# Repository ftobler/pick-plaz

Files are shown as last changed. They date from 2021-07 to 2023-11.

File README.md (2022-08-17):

# pick-plaz
Open source pick and place machine

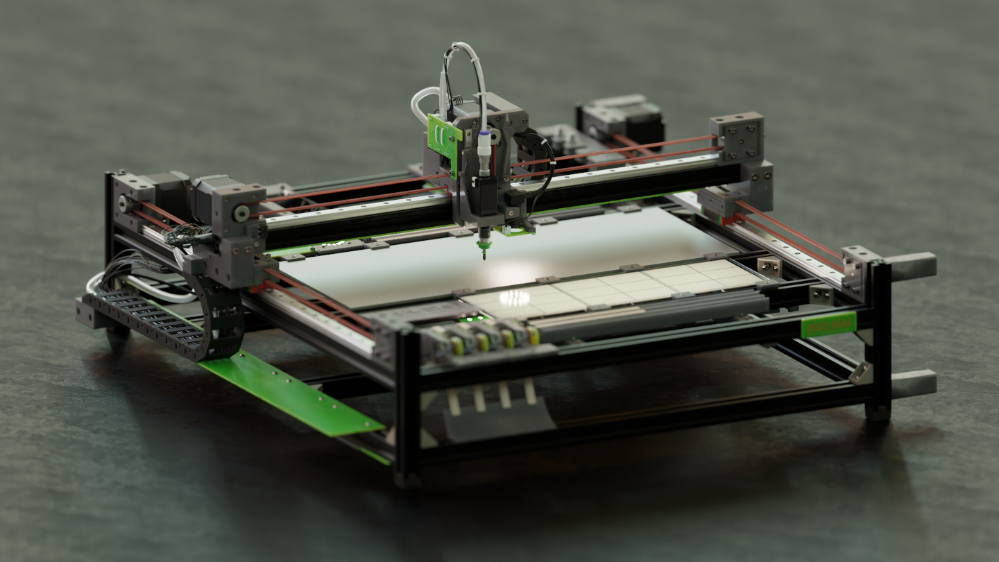
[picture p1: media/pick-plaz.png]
CAD Image Pick-Plaz


[CAD Onshape](https://cad.onshape.com/documents/175bb45940c329c46a77df39/w/56e16a8885c2fef63520b9e2/e/e7ab10496d879b6cf281b14f)

[STEP file repostory (CAD)](https://github.com/ftobler/pick-plaz-cad)

[More Pictures (Imgur)](https://imgur.com/a/lOQ79OQ)

## Issues

* Part preview missing zero point of ICs

# Wishlist

* Camera sharpen menu in UI (laplacian of camera image)

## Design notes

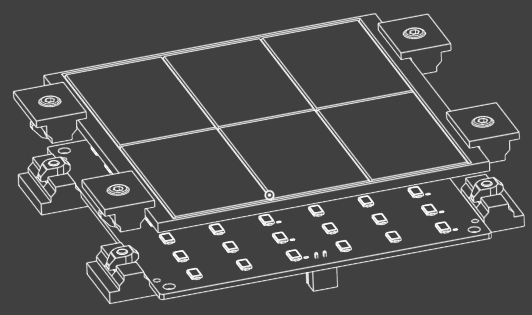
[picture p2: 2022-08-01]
python/web/img/tray.png

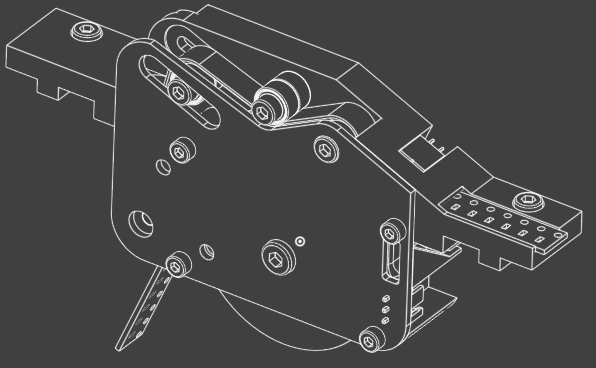
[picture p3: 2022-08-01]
python/web/img/roll.png

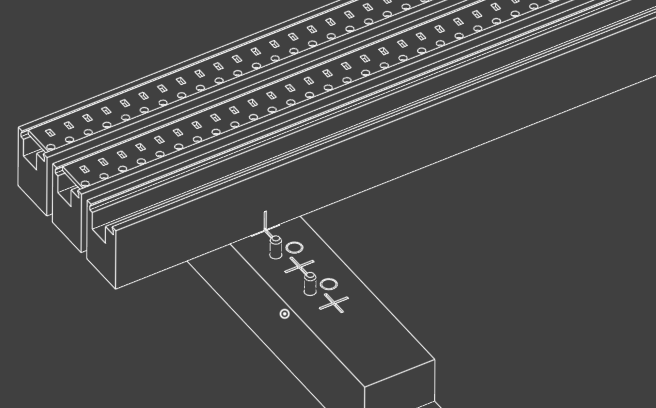
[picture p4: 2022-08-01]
python/web/img/belt.png

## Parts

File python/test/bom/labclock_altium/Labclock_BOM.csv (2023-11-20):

Designator | Quantity | GPV_Number | Description | Manufacturer | Manufacturer Part Number | Footprint
C1, C2 | 2 | 1749.0090 | Cap Cer SMD 10p 50V +/- 0.25pF 0603 C0G | AVX | 06035A100CAT* | C-0603_1608_095_L_RF
C3, C4, C5, C6, C7, C8, C9 | 7 | 1749.0196 | Cap Cer SMD 100n 100V 10% 0603 X7R | MURATA | GRM188R72A104KA35 | C-0603_1608_095_L_RF
D1 | 1 | xxxx.xxxx | IC MCU Cortex M0+ 32K Flash, 8K RAM, 64MHz | ST | STM32G030F6P6 | TSSOP20_N_RF
G1 | 1 | xxxx.xxxx | Crystal Oscillator 32.768kHz 12.5pF �20ppm | ABEL ELECTRON | SMD-3215_2P32.768KHZ12.5PF10PPM | G_3215_N_RF
IC1 | 1 | xxxx.xxxx | IC Converter USB UART | WCN | CH340C | SOIC16_N_RF
R1, R2, R3, R4, R5, R6, R7, R8 | 8 | 1922.0102 | Res SMD 100R 1% 0.1W 0603 | YAGEO | RC0603FR-07100RL | R-0603_1608_050_L_RF
R9, R10, R11, R12, R13, R14, R15, R16, R18, R19, R20, R21, R22, R23, R24, R25, R26, R27, R28, R29, R30, R31, R32, R33, R34, R35 | 26 | 1922.0100 | Res SMD 10k 1% 0.1W 0603 | YAGEO | RC0603FR-0710KL | R-0603_1608_050_L_RF
R17, R36 | 2 | 1922.0011 | Res SMD 1k 1% 0.1W 0603 | YAGEO | RC0603FR-071KL | R-0603_1608_050_L_RF
R37 | 1 | 1922.0140 | Res SMD 100k 1% 0.1W 0603 | YAGEO | RC0603FR-07100KL | R-0603_1608_050_L_RF
U1 | 1 | 1500.7299 | IC REG LDO 3.3V 0.8A SOT223 | Texas Instruments | LM1117MPX-3.3/NOPB | SOT223_L_RF
V1 | 1 | xxxx.xxxx | LED 7-Segment 38mm x 45mm | ? | FJS18101AH | FJS18101AH
V2, V3, V4, V5, V6, V7, V8, V9 | 8 | 1601.0679 | TRANS SMD PNP -45V -0.1A BC807-40 SOT23 | NXP Semiconductors | BC807-40 | SOT23_L_RF
V10 | 1 | 1601.1733 | MOSFET N-CH 50V 200MA SOT-23 | onsemi | BSS138LT1G | SOT23_L_RF
V11, V12, V13, V14, V15, V16, V17, V18, V21 | 9 | 1601.0512 | TRANS SMD NPN 45V 0.1A BC847B SOT23 | NXP Semiconductors | BC847B/C | SOT23_L_RF
V19 | 1 | 1600.2395 | Diode Schottky 20V 0.5A SOD123 | ONSemi | MBR0520LT1G | SOD123_L_RF
V20 | 1 |  | Diode Schottky 1mA 40 Volt | VISHAY | SD101CW-E3-08 | SOD123_L_RF
V29 | 1 | xxxx.xxxx | RGB LED SPI Interface | APA Electronic CO | APA-102-2020-256-8A | V_2020_P6_N_RF
X1, X2 | 2 |  | CONN HEADER 5POS 1ROW THT 2.54MM WE 61300511121 | W�rth Elektronik | 61300511121 | X-0127X0025_R_WE_61300511121
X3 | 1 | xxxx.xxxx | CONN USB-C 16pin | Molex | 105450-0101 | 105450-0101

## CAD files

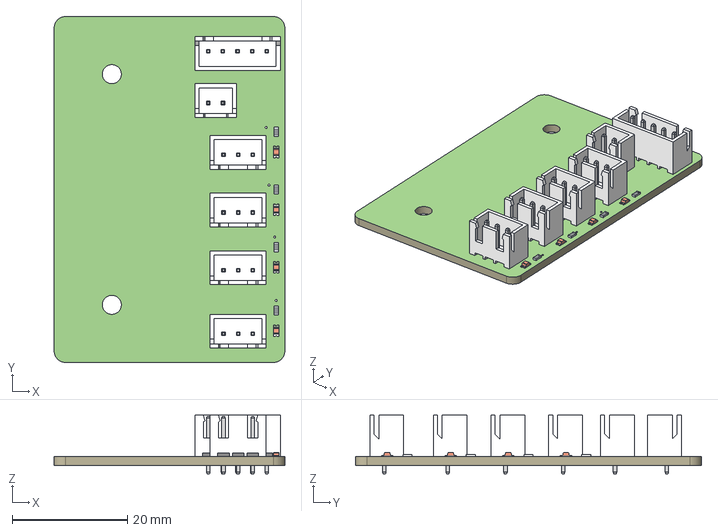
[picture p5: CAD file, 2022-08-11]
pcb/pcb-pick-plaz-feeder-wiring/pcb-pick-plaz-feeder-wiring.step
40.0 x 60.0 x 10.2 mm

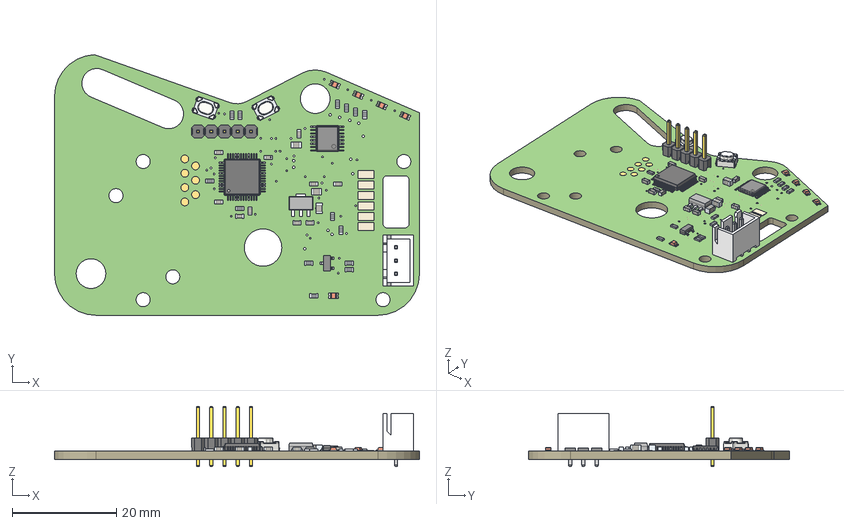
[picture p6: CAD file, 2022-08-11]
pcb/pcb-pick-plaz-feeder/pcb-pick-plaz-feeder.step
70.0 x 50.0 x 11.6 mm

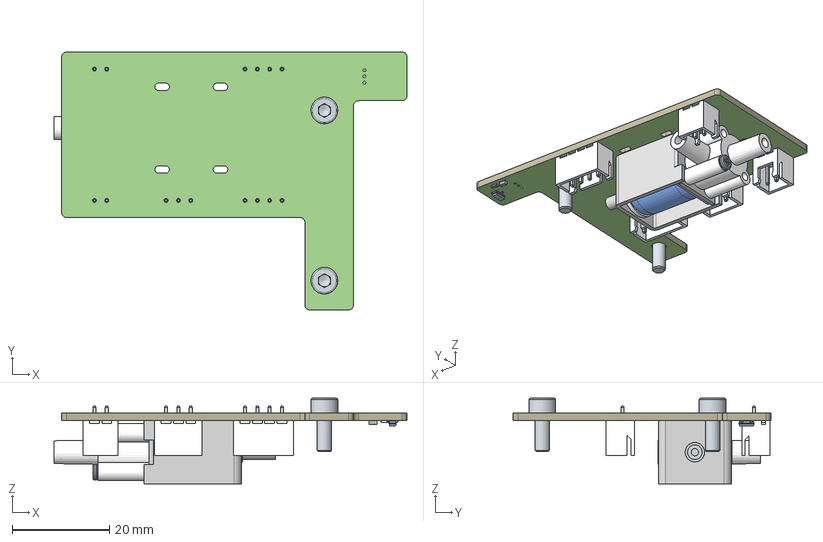
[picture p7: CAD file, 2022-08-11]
pcb/pcb-pick-plaz-hall/pcb hall.step
72.6 x 53.0 x 17.6 mm
Hex socket head cap screw M3x0.50 x 8 x 2
B4B-XH
B3B-XH
Board
B2B-XH
SOT-23
B4B-XH_1
0603-RES
0603_CAP
B2B-XH_1
solenoid valve

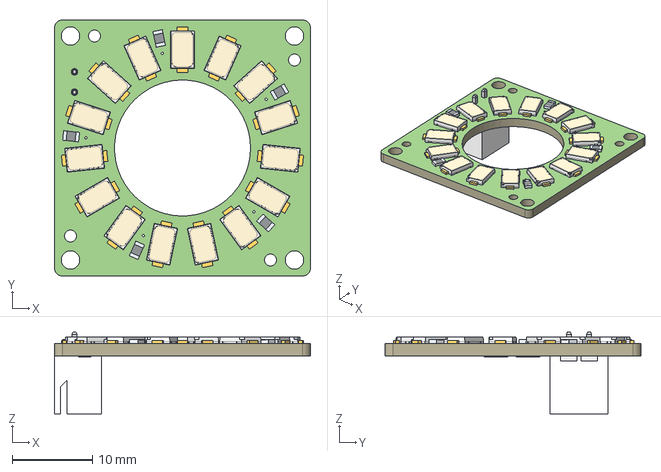
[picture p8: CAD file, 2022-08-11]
pcb/pcb-pick-plaz-ring/pcb-pick-plaz-ring eagle.step
32.0 x 32.0 x 10.2 mm

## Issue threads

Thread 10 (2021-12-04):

Split Screen GUI / Camera

ftobler, 2021-12-04:
Request to add the Option to view the GUI Splitscreen with the camera always on one side of the screen.

8wangyuyang, 2024-04-24:
没有标注用什么上位机软件控制,求软件名。谢谢！

ftobler, 2024-04-28:
Not sure what you mean. The software is the python stuff in this repository. All custom.

8wangyuyang, 2024-04-28:
我的意思是上位机，就像开源的OpenPnP贴片上位机软件。这个是用的是树莓派3B做上位机，用的什么系统或上位机。求大佬资料教程，谢谢！大佬的开源。PCB板已打样，只缺软件控制界面或软件。感谢😊😊😊

8wangyuyang, 2024-04-28:
python调用camera，gui界面 是吗？

ftobler, 2024-04-28:
This is not a OpenPnP build. Python does run on a raspberry pi as host, but you can use other hosts as well. The camera is a standard webcam, the GUI is on the webserver.

8wangyuyang, 2024-04-28:
不支持OpenPNP软件，GUI位于网络服务器是网址或IP地址是吗？

8wangyuyang, 2024-04-28:
我是第一次制作贴片机在树莓派运行的，我安装过klipper不知道一样吗？

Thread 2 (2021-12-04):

Reset Fiducial Placement

ftobler, 2021-12-04:
Request to add a function to reset all fiducial for a new pcb.

ftobler, 2022-07-30:
done

Closed 2022-07-30.

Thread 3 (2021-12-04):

Reset Part Placement

ftobler, 2021-12-04:
Request to add a function to reset part status to place a new pcb

ftobler, 2022-07-30:
done

Closed 2022-07-30.

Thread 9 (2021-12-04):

Improve Auto Assignment of Symbols

ftobler, 2021-12-04:
When PNP and BOM is loaded, the software automatically sets the symbols for the most common package types. This does not work for the following examples:

- SOIC-16

ftobler, 2022-01-23:
in footprints.json there is now a alternative ("alt") list where the parser is looking for a match.

match is made withoug special characters like '-' and '_'

Closed 2022-01-23.

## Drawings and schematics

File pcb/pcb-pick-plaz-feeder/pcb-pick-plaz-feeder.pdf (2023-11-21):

# GND ¹⁰u

## DRV8833PWPR

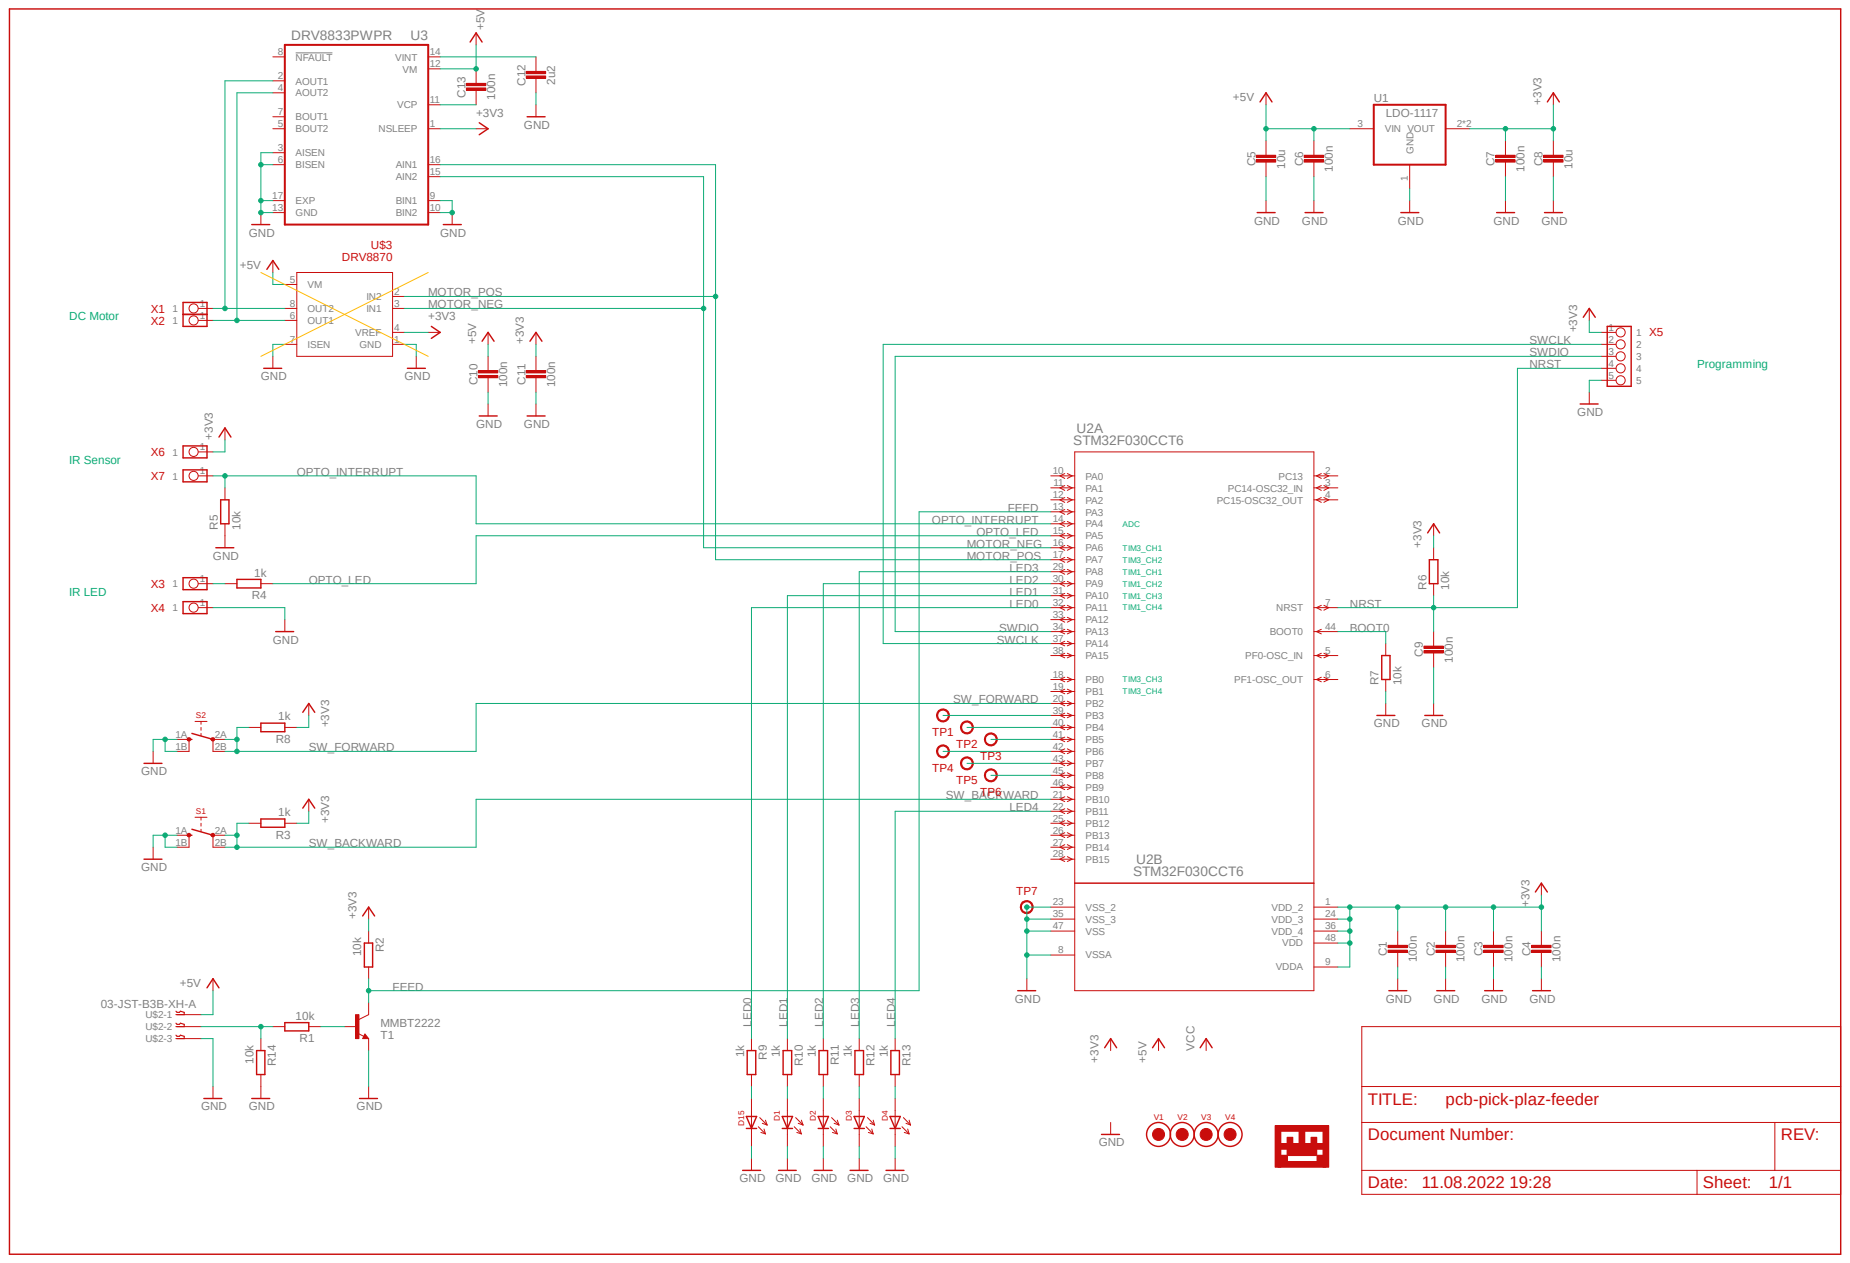
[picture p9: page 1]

MOTOR_NEG | PA6 16
MOTOR_POS | PA7 17

LED3 | PA8 29

PA9 30
PA10 31
PA11 32

SWDIO | PA12 33 PA13 34 | BOOT0

pcb-pick-plaz-feeder

Document Number: | REV:

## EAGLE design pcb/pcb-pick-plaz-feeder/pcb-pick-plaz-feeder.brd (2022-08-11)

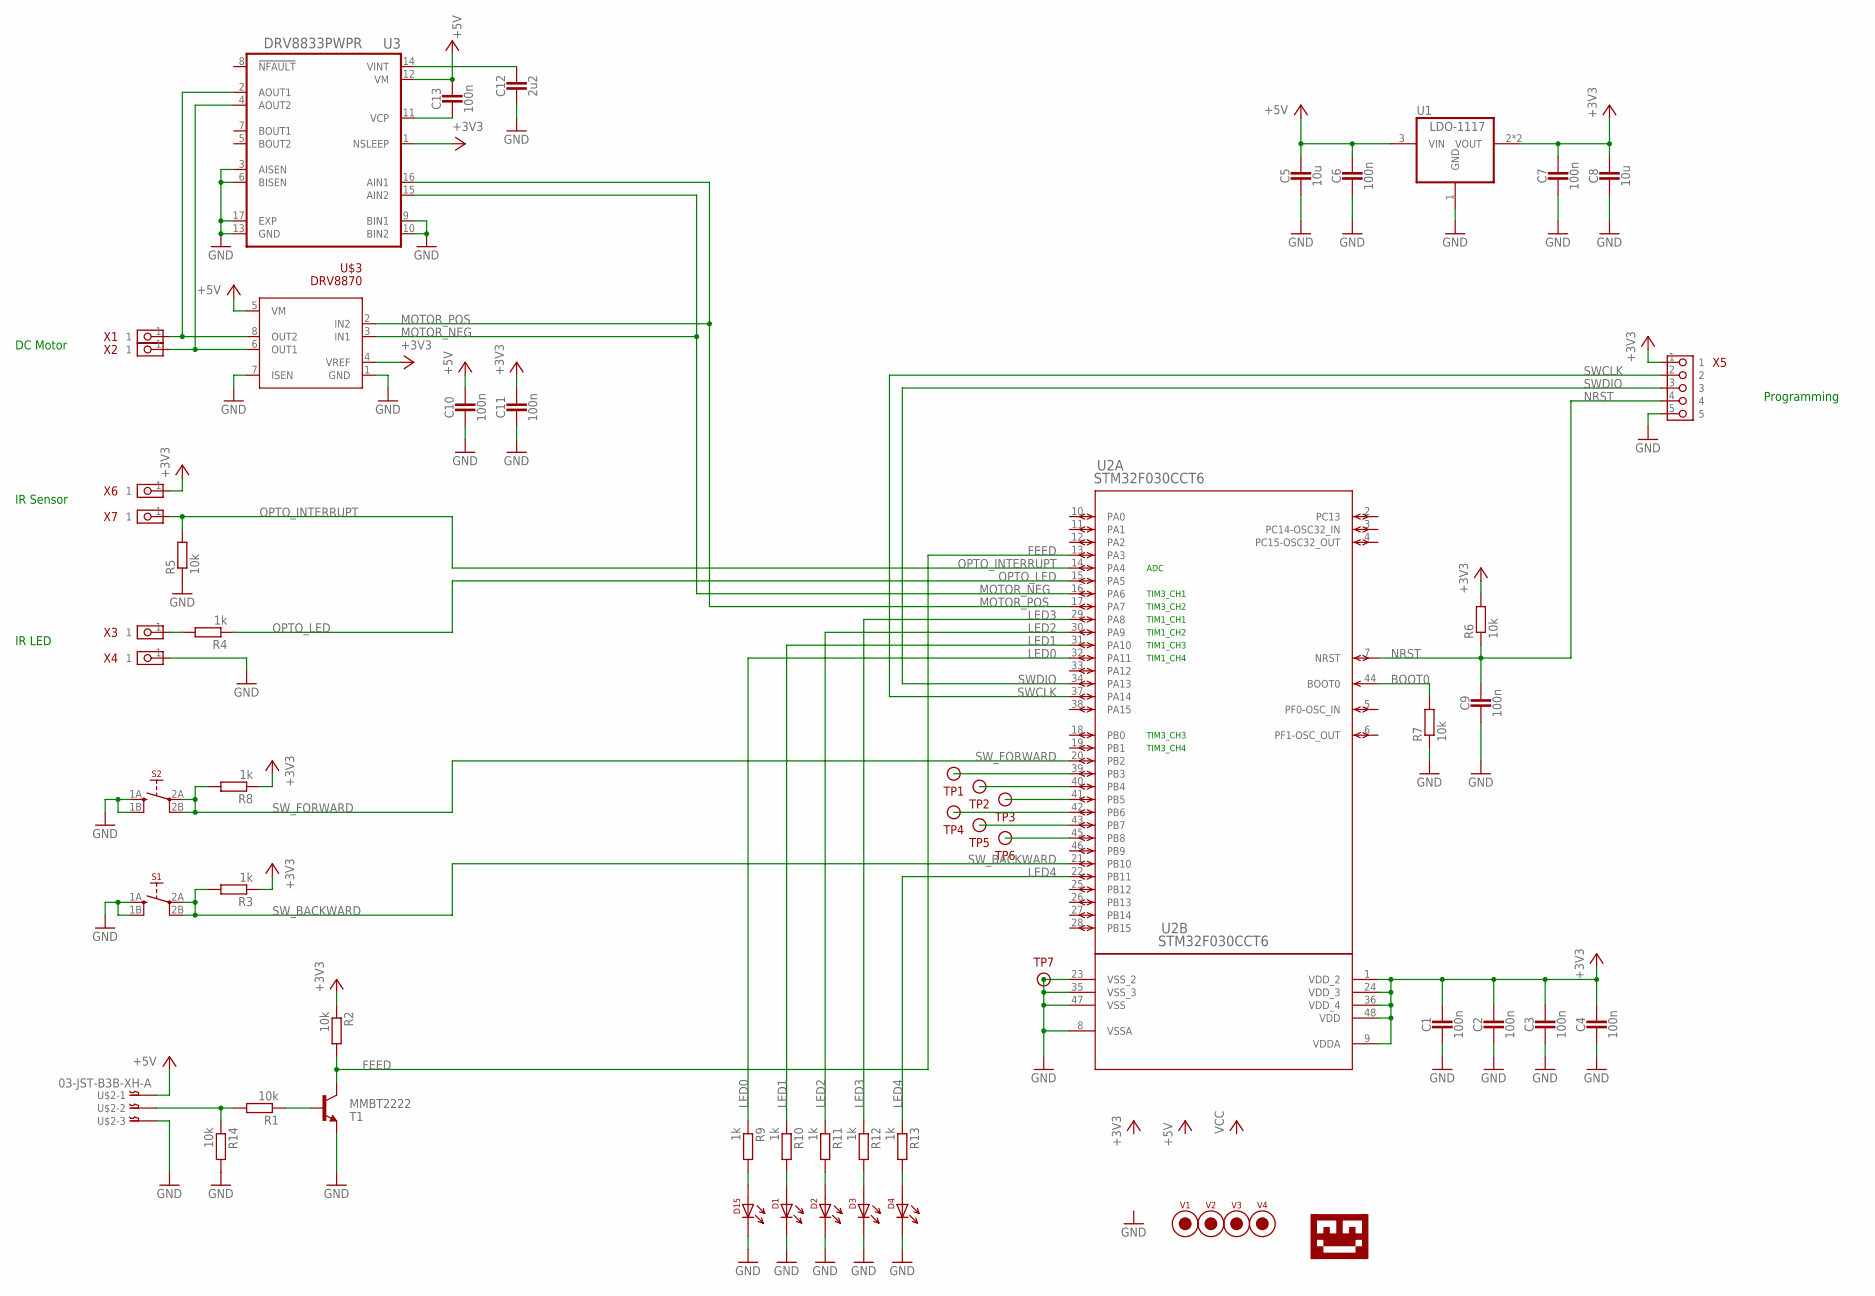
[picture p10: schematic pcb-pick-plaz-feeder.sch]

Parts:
C1, C2, C3, C4, C6, C7, C9, C10, C11, C13: 100n; 0603_CAP
C5, C8: 10u; 0805_CAP
C12: 2u2; 0805_CAP
D1, D2, D3, D4, D15: LED-0805; 0805-DOT
R1, R2, R5, R6, R7, R14: 10k; 0603-RES
R3, R4, R8, R9, R10, R11, R12, R13: 1k; 0603-RES
S1, S2: SWITCH_2PD; SWITCH_WH
T1: MMBT2222; SOT23-BEC
TP1, TP2, TP3, TP4, TP5, TP6, TP7: TESTPIN; PIN-SMD-1X1-TEST_1M5
U1: LDO-1117; SOT-89
U2: STM32F030CCT6; LQFP48-7X7MM
U3: DRV8833PWPR; IC_DRV8833PWPR
U$1: LOGO-TOBENG-1MM-FINISH; TOBENG-1MM-FINISH
U$2: 03-JST-B3B-XH-A; B3B-XH
U$3: DRV8870; SOIC-8
V1, V2, V3, V4: FIDUCIAL2MM; FIDUCIAL_2MM
X1, X2, X3, X4, X6, X7: PIN_1X1SMD_BIG_L; PIN_1X1_SMD_BIG_L
X5: PIN_5X1HD; PIN_5X1_HD

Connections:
+3V3: C1.1, C2.1, C3.1, C4.1, C7.1, C8.P$1 (1), C11.1, R2.1, R3.1, R6.2, R8.1, U1.2 (VOUT), U1.2@1 (VOUT), U2.1 (VDD_2), U2.9 (VDDA), U2.24 (VDD_3), U2.36 (VDD_4), U2.48 (VDD), U3.1 (NSLEEP), U$3.4 (VREF), X5.1, X6.1
+5V: C5.P$1 (1), C6.1, C10.1, C13.1, U1.3 (VIN), U3.12 (VM), U$2.P$1, U$3.5 (VM)
BOOT0: R7.2, U2.44 (BOOT0)
FEED: R2.2, T1.C, U2.13 (PA3)
GND: C1.2, C2.2, C3.2, C4.2, C5.P$2 (2), C6.2, C7.2, C8.P$2 (2), C9.2, C10.2, C11.2, C12.P$2 (2), D1.2, D2.2, D3.2, D4.2, D15.2, R5.1, R7.1, R14.2, S1.1A (1), S1.1B (2), S2.1A (1), S2.1B (2), T1.E, TP7.1, U1.1 (GND), U2.8 (VSSA), U2.23 (VSS_2), U2.35 (VSS_3), U2.47 (VSS), U3.3 (AISEN), U3.6 (BISEN), U3.9 (BIN1), U3.10 (BIN2), U3.13 (GND), U3.17 (EXP), U$2.P$3, U$3.1 (GND), U$3.7 (ISEN), X4.1, X5.5
LED0: R9.1, U2.32 (PA11)
LED1: R10.1, U2.31 (PA10)
LED2: R11.1, U2.30 (PA9)
LED3: R12.1, U2.29 (PA8)
LED4: R13.1, U2.22 (PB11)
MOTOR_NEG: U2.16 (PA6), U3.15 (AIN2), U$3.3 (IN1)
MOTOR_POS: U2.17 (PA7), U3.16 (AIN1), U$3.2 (IN2)
unnamed: U3.4 (AOUT2), U$3.6 (OUT1), X2.1
unnamed: U3.2 (AOUT1), U$3.8 (OUT2), X1.1
unnamed: R1.2, R14.1, U$2.P$2
unnamed: R1.1, T1.B
unnamed: R4.2, X3.1
unnamed: D15.1, R9.2
unnamed: D1.1, R10.2
unnamed: D2.1, R11.2
unnamed: D3.1, R12.2
unnamed: D4.1, R13.2
unnamed: TP1.1, U2.39 (PB3)
unnamed: TP2.1, U2.40 (PB4)
unnamed: TP3.1, U2.41 (PB5)
unnamed: TP4.1, U2.42 (PB6)
unnamed: TP5.1, U2.43 (PB7)
unnamed: TP6.1, U2.45 (PB8)
unnamed: C12.P$1 (1), U3.14 (VINT)
unnamed: C13.2, U3.11 (VCP)
NRST: C9.1, R6.1, U2.7 (NRST), X5.4
OPTO_INTERRUPT: R5.2, U2.14 (PA4), X7.1
OPTO_LED: R4.1, U2.15 (PA5)
SWCLK: U2.37 (PA14), X5.2
SWDIO: U2.34 (PA13), X5.3
SW_BACKWARD: R3.2, S1.2A (3), S1.2B (4), U2.21 (PB10)
SW_FORWARD: R8.2, S2.2A (3), S2.2B (4), U2.20 (PB2)

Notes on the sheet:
Programming
DC Motor
IR LED
IR Sensor
ADC
TIM1_CH1
TIM1_CH2
TIM3_CH1
TIM3_CH2
TIM3_CH3
TIM3_CH4
TIM1_CH3
TIM1_CH4

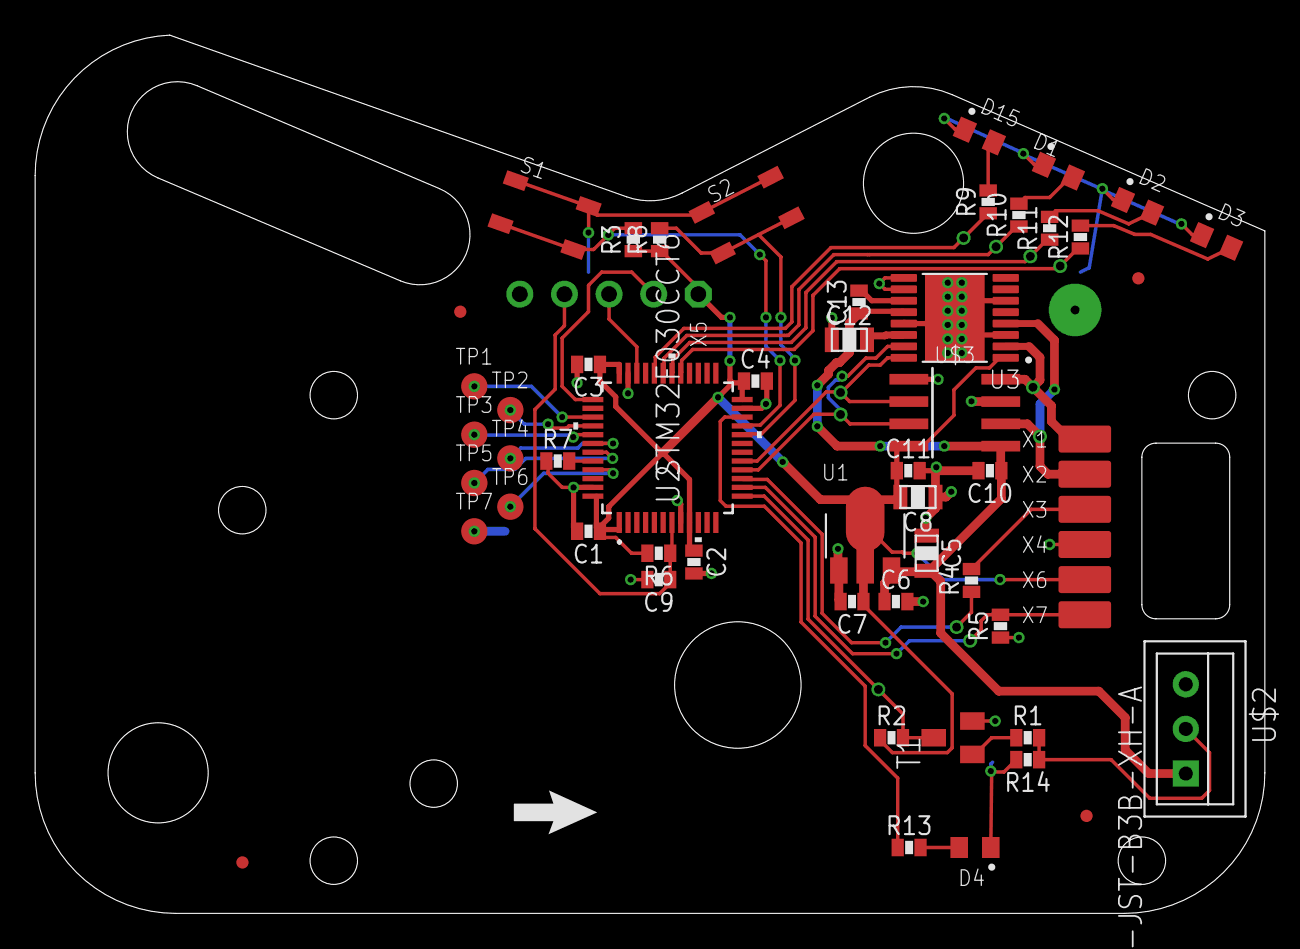
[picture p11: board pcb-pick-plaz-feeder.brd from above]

Board: 2 copper layers, 70.0 x 50.0 mm, 59 parts (0 on the bottom side), 37 nets.

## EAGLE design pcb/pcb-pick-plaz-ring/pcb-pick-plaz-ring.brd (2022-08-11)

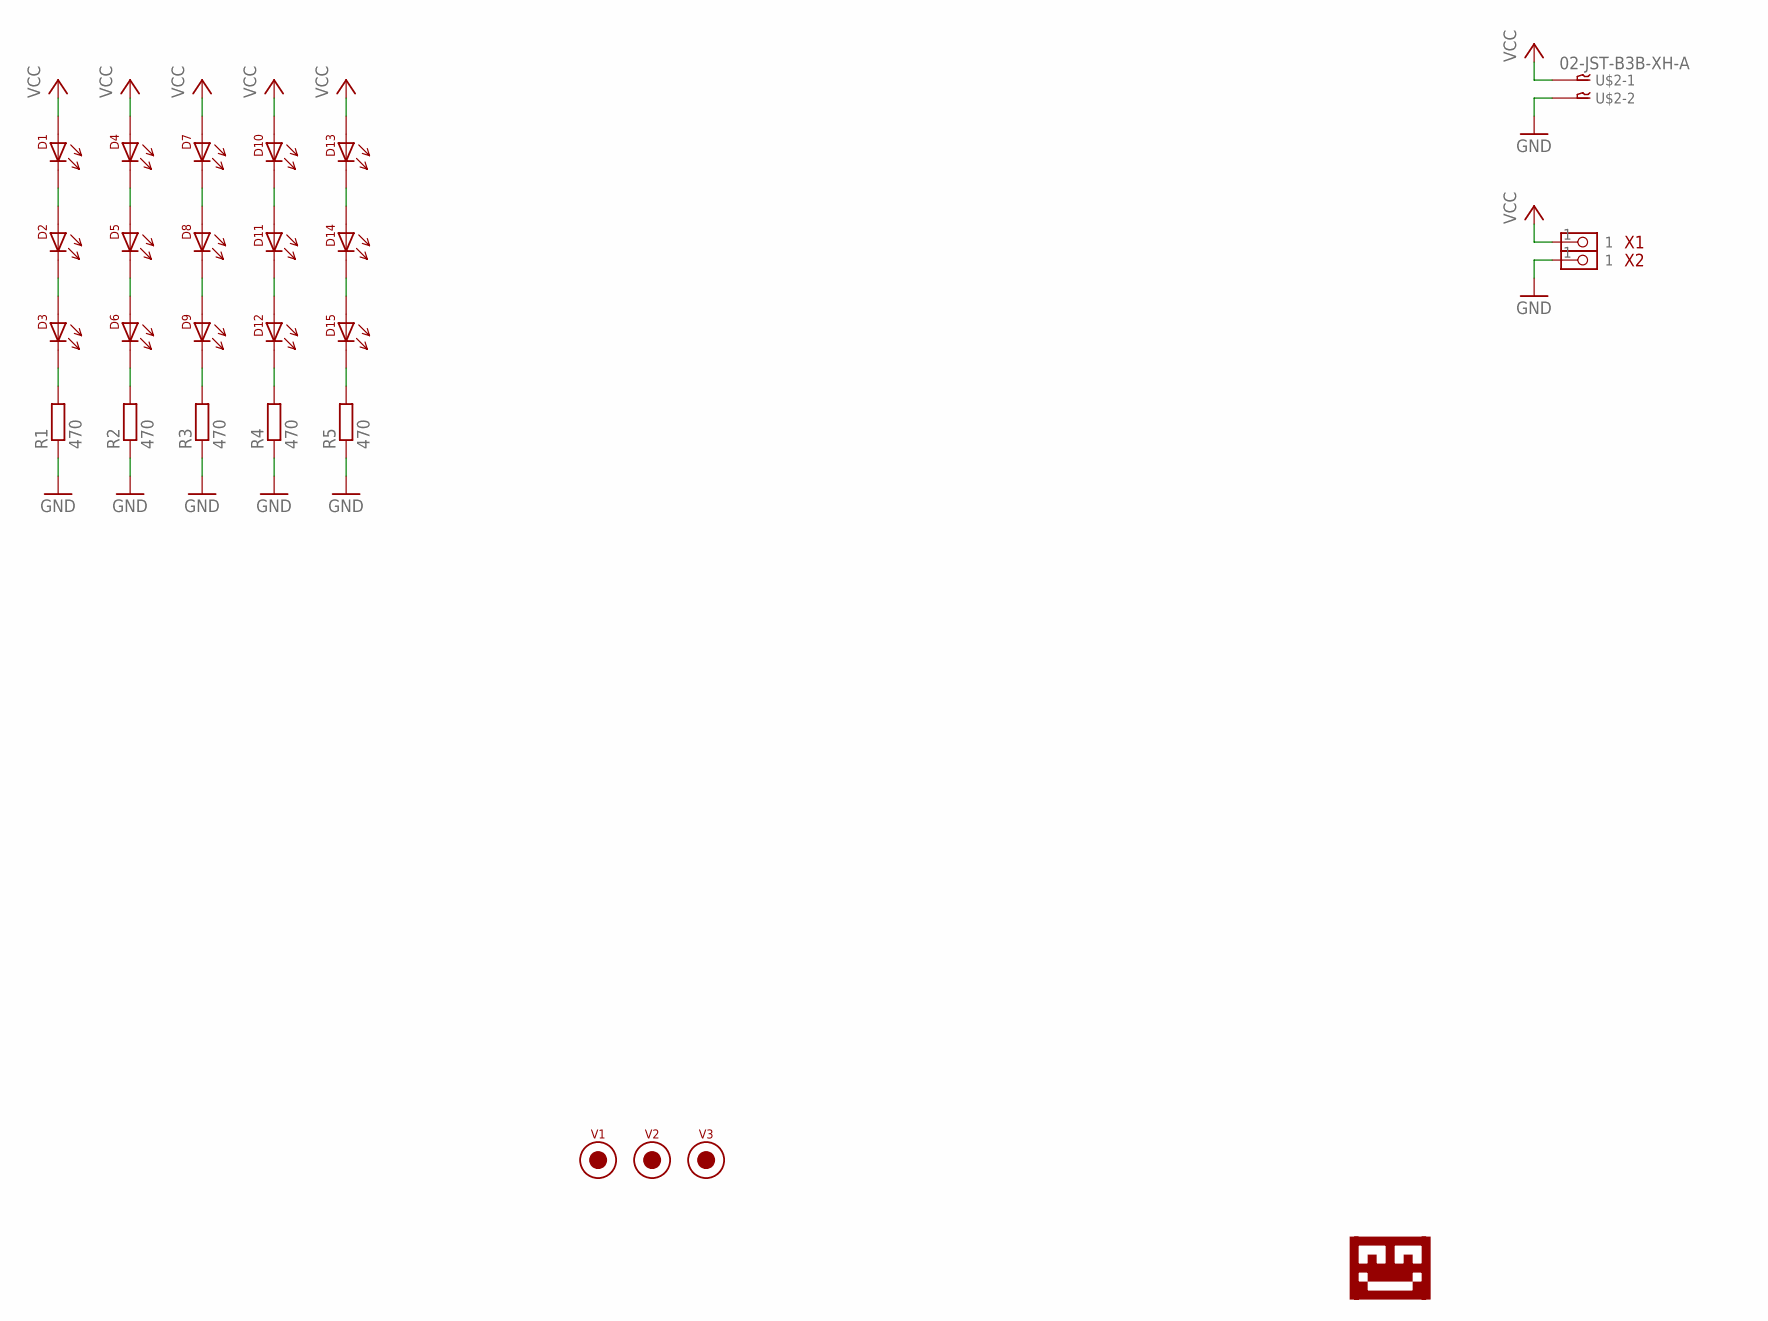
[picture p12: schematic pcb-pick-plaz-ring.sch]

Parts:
D1, D2, D3, D4, D5, D6, D7, D8, D9, D10, D11, D12, D13, D14, D15: LED-5730; 5730-LED
R1, R2, R3, R4, R5: 470; 0805_RES
U$1: LOGO-TOBENG-1MM-FINISH; TOBENG-1MM-FINISH
U$2: 02-JST-B3B-XH-A; B2B-XH
V1, V2, V3: FIDUCIAL2MM; FIDUCIAL_2MM
X1, X2: PIN_1X1SMD_BIG_L; PIN_1X1_SMD_BIG_L

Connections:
GND: R1.1, R2.1, R3.1, R4.1, R5.1, U$2.P$2, X2.1
unnamed: D1.C (2), D2.A1 (1), D2.A2 (1)
unnamed: D2.C (2), D3.A1 (1), D3.A2 (1)
unnamed: D3.C (2), R1.2
unnamed: D4.C (2), D5.A1 (1), D5.A2 (1)
unnamed: D5.C (2), D6.A1 (1), D6.A2 (1)
unnamed: D6.C (2), R2.2
unnamed: D7.C (2), D8.A1 (1), D8.A2 (1)
unnamed: D8.C (2), D9.A1 (1), D9.A2 (1)
unnamed: D9.C (2), R3.2
unnamed: D10.C (2), D11.A1 (1), D11.A2 (1)
unnamed: D11.C (2), D12.A1 (1), D12.A2 (1)
unnamed: D12.C (2), R4.2
unnamed: D13.C (2), D14.A1 (1), D14.A2 (1)
unnamed: D14.C (2), D15.A1 (1), D15.A2 (1)
unnamed: D15.C (2), R5.2
VCC: D1.A1 (1), D1.A2 (1), D4.A1 (1), D4.A2 (1), D7.A1 (1), D7.A2 (1), D10.A1 (1), D10.A2 (1), D13.A1 (1), D13.A2 (1), U$2.P$1, X1.1

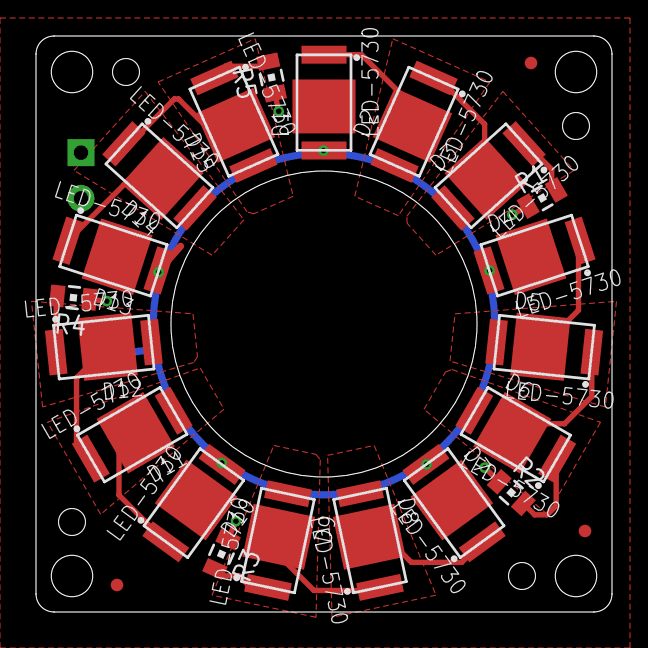
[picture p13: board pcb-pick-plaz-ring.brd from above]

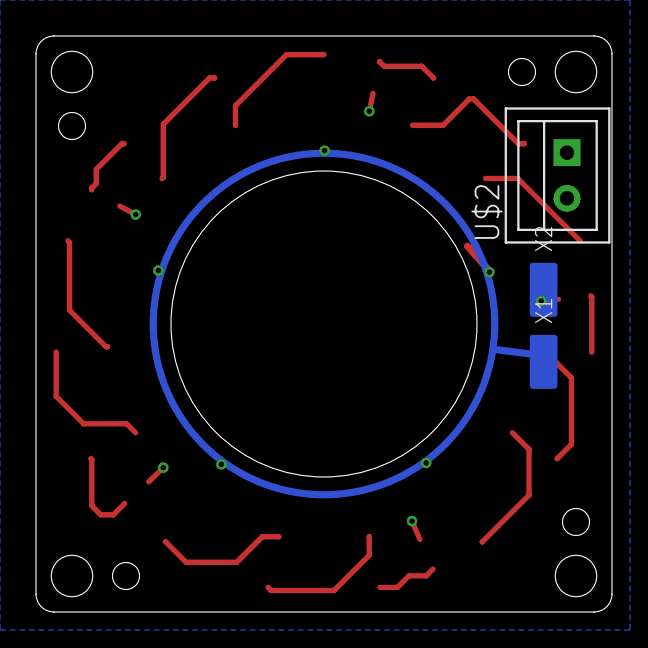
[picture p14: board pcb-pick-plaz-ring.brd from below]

Board: 2 copper layers, 32.0 x 32.0 mm, 27 parts (4 on the bottom side), 17 nets.

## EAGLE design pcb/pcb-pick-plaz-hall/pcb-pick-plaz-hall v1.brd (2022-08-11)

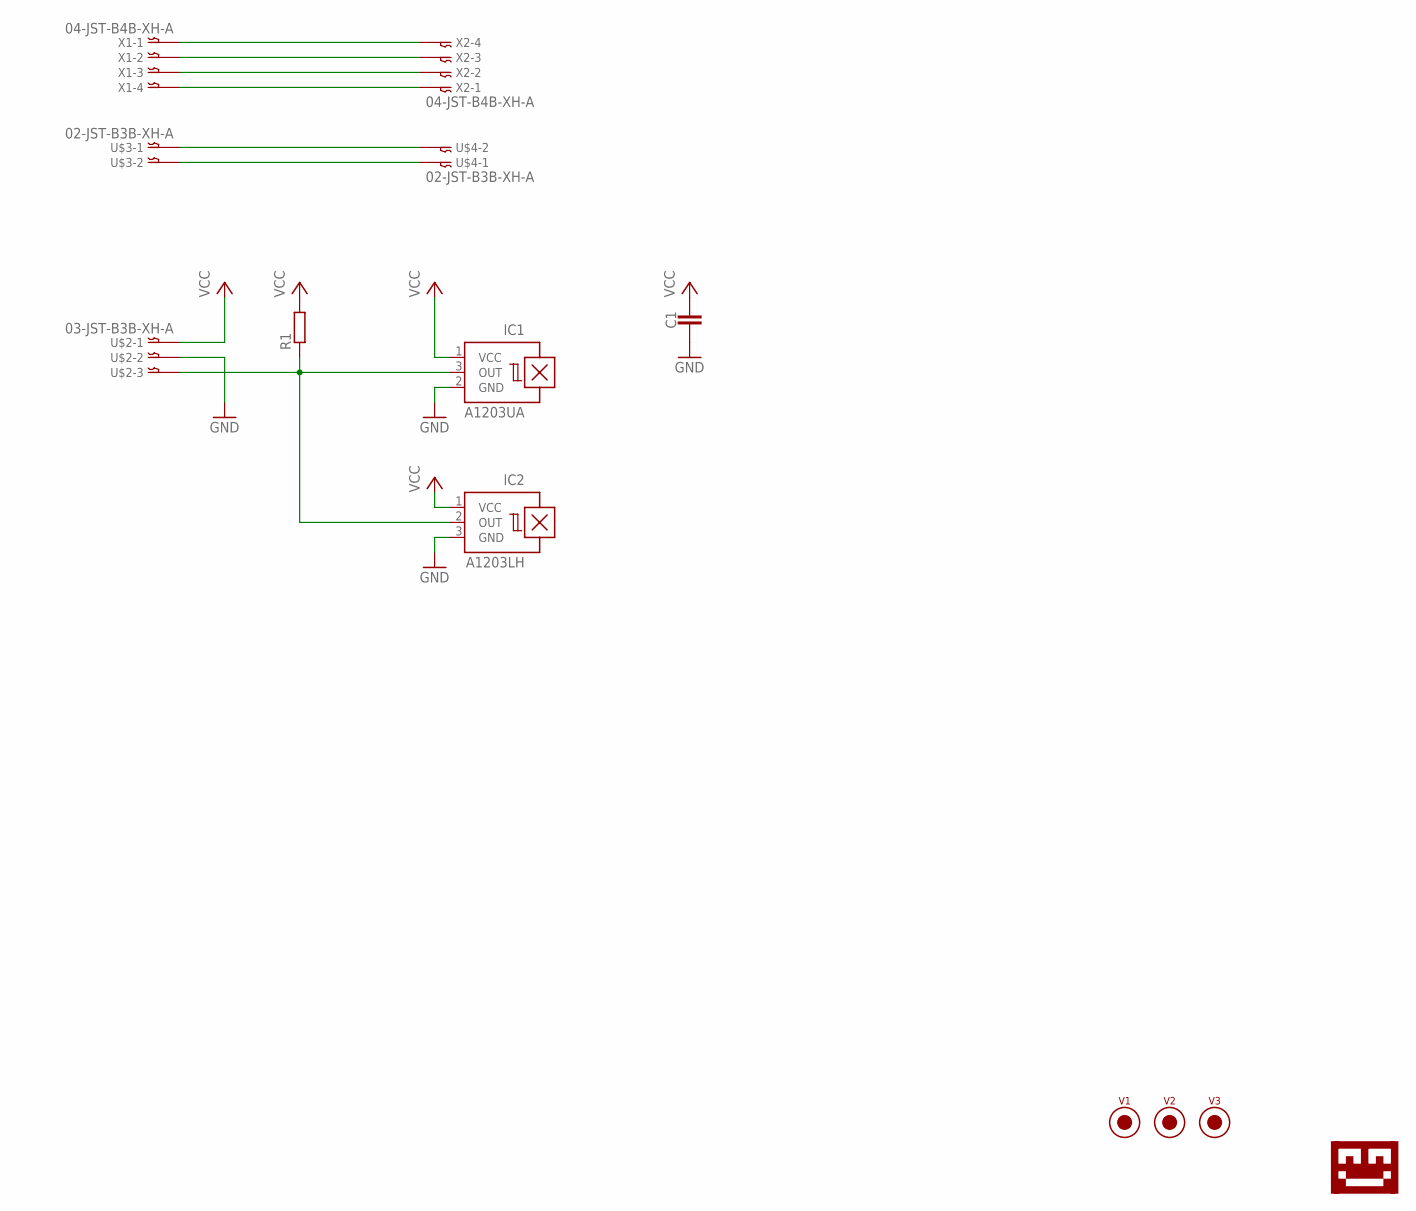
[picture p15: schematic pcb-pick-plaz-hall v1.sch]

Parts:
C1: CAPACITOR0603_CAP; 0603_CAP
IC1: A1203UA; SIP3-UA
IC2: A1203LH; SOT23-W
R1: RESISTOR0603_RES; 0603-RES
U$1: LOGO-TOBENG-1MM; TOBENG-1MM
U$2: 03-JST-B3B-XH-A; B3B-XH
U$3, U$4: 02-JST-B3B-XH-A; B2B-XH
V1, V2, V3: FIDUCIAL2MM; FIDUCIAL_2MM
X1, X2: 04-JST-B4B-XH-A; B4B-XH

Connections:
GND: C1.2, IC1.2 (GND), IC2.3 (GND), U$2.P$2
unnamed: X1.P$1, X2.P$4
unnamed: X1.P$2, X2.P$3
unnamed: X1.P$3, X2.P$2
unnamed: X1.P$4, X2.P$1
unnamed: U$3.P$1, U$4.P$2
unnamed: U$3.P$2, U$4.P$1
unnamed: IC1.3 (OUT), IC2.2 (OUT), R1.1, U$2.P$3
VCC: C1.1, IC1.1 (VCC), IC2.1 (VCC), R1.2, U$2.P$1

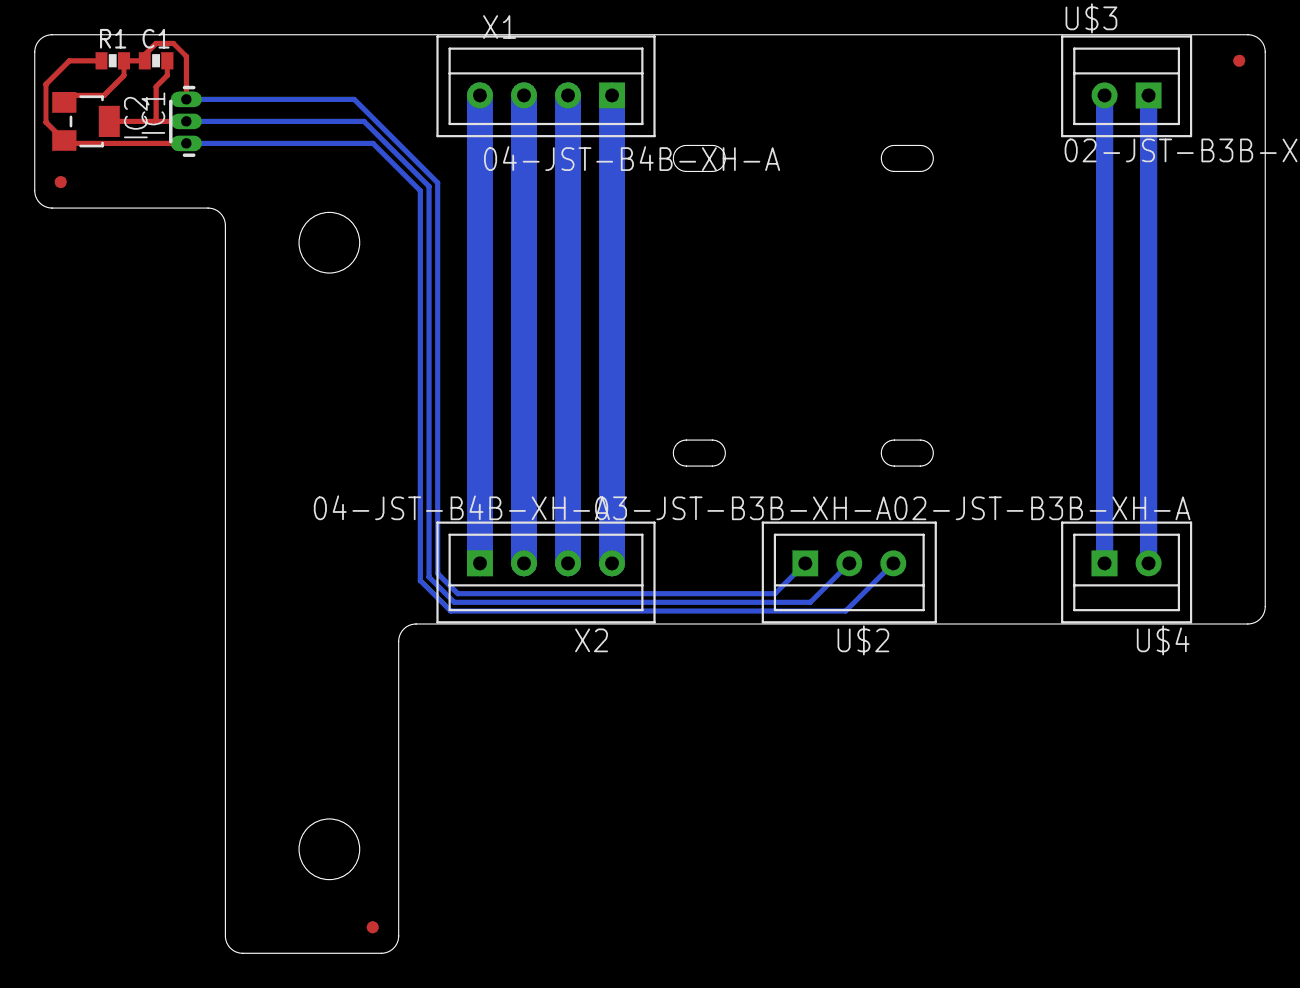
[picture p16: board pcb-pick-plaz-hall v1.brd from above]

Board: 2 copper layers, 71.0 x 53.0 mm, 13 parts (1 on the bottom side), 9 nets.

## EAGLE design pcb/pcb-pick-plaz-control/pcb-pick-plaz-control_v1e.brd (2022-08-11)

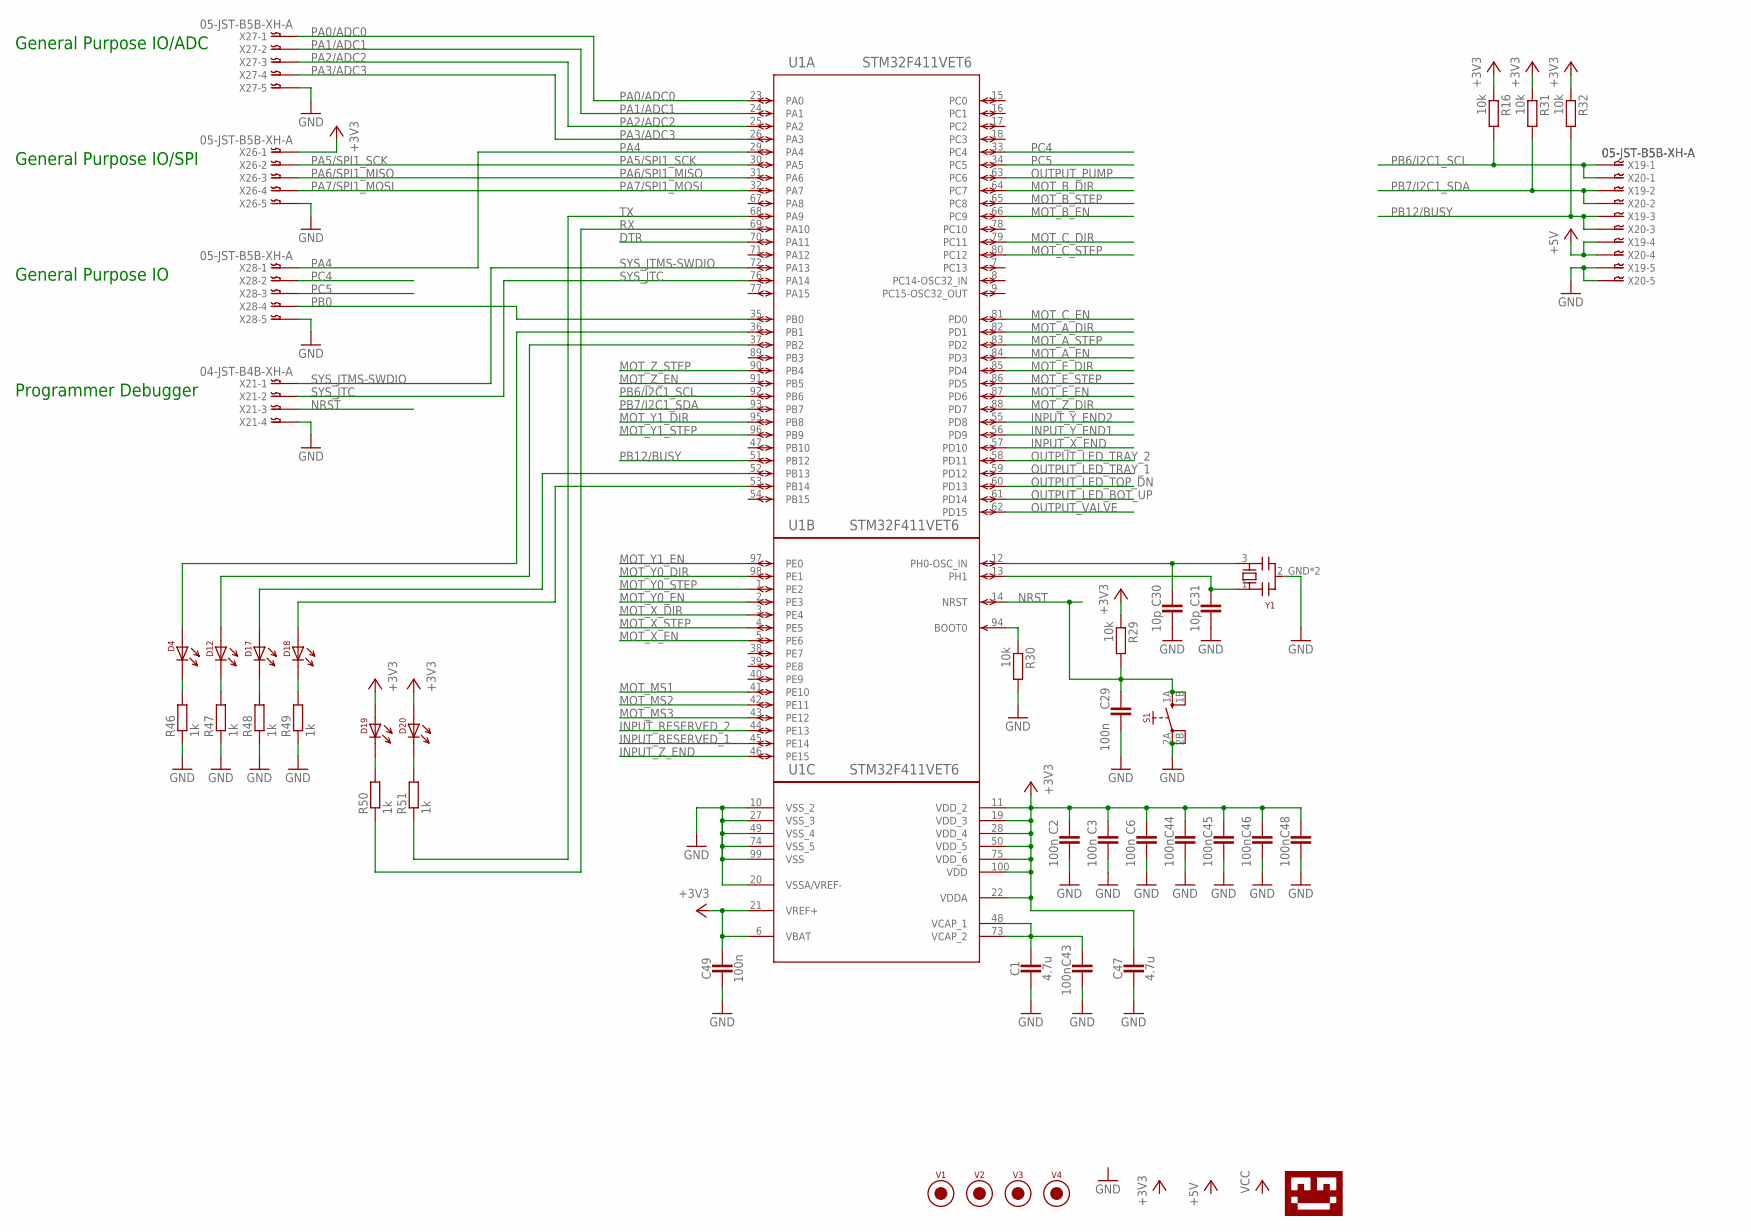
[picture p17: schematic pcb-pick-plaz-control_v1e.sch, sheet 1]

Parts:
C1, C47: 4.7u; 0805_CAP
C2, C3, C6, C29, C43, C44, C45, C46, C48, C49: 100n; 0603_CAP
C30, C31: 10p; 0603_CAP
D4, D12, D17, D18, D19, D20: LED-0805; 0805-DOT
R16, R29, R30, R31, R32: 10k; 0603-RES
R46, R47, R48, R49, R50, R51: 1k; 0603-RES
S1: SWITCH_2PD; SWITCH_WH
U1: STM32F411VET6; LQFP100-14X14MM
U$1: LOGO-TOBENG-1MM-FINISH; TOBENG-1MM-FINISH
V1, V2, V3, V4: FIDUCIAL2MM; FIDUCIAL_2MM
X19, X20, X26, X27, X28: 05-JST-B5B-XH-A; B5B-XH
X21: 04-JST-B4B-XH-A; B4B-XH
Y1: 3213-QUARZ3225; 3225-QUARZ

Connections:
+3V3: C2.1, C3.1, C6.1, C44.1, C45.1, C46.1, C47.P$1 (1), C48.1, C49.1, D19.1, D20.1, R16.1, R29.1, R31.1, R32.1, U1.6 (VBAT), U1.11 (VDD_2), U1.19 (VDD_3), U1.21 (VREF+), U1.22 (VDDA), U1.28 (VDD_4), U1.50 (VDD_5), U1.75 (VDD_6), U1.100 (VDD), X26.P$1; also elsewhere on the board
+5V: X19.P$4, X20.P$4; also elsewhere on the board
DTR: U1.70 (PA11); also elsewhere on the board
GND: C1.P$2 (2), C2.2, C3.2, C6.2, C29.2, C30.2, C31.2, C43.2, C44.2, C45.2, C46.2, C47.P$2 (2), C48.2, C49.2, R30.2, R46.1, R47.1, R48.1, R49.1, S1.2A (3), S1.2B (4), U1.10 (VSS_2), U1.20 (VSSA/VREF-), U1.27 (VSS_3), U1.49 (VSS_4), U1.74 (VSS_5), U1.99 (VSS), X19.P$5, X20.P$5, X21.P$4, X26.P$5, X27.P$5, X28.P$5, Y1.2_GND (2), Y1.4_GND (2); also elsewhere on the board
INPUT_RESERVED_1: U1.45 (PE14); also elsewhere on the board
INPUT_RESERVED_2: U1.44 (PE13); also elsewhere on the board
INPUT_X_END: U1.57 (PD10); also elsewhere on the board
INPUT_Y_END1: U1.56 (PD9); also elsewhere on the board
INPUT_Y_END2: U1.55 (PD8); also elsewhere on the board
INPUT_Z_END: U1.46 (PE15); also elsewhere on the board
MOT_A_DIR: U1.82 (PD1); also elsewhere on the board
MOT_A_EN: U1.84 (PD3); also elsewhere on the board
MOT_A_STEP: U1.83 (PD2); also elsewhere on the board
MOT_B_DIR: U1.64 (PC7); also elsewhere on the board
MOT_B_EN: U1.66 (PC9); also elsewhere on the board
MOT_B_STEP: U1.65 (PC8); also elsewhere on the board
MOT_C_DIR: U1.79 (PC11); also elsewhere on the board
MOT_C_EN: U1.81 (PD0); also elsewhere on the board
MOT_C_STEP: U1.80 (PC12); also elsewhere on the board
MOT_E_DIR: U1.85 (PD4); also elsewhere on the board
MOT_E_EN: U1.87 (PD6); also elsewhere on the board
MOT_E_STEP: U1.86 (PD5); also elsewhere on the board
MOT_MS1: U1.41 (PE10); also elsewhere on the board
MOT_MS2: U1.42 (PE11); also elsewhere on the board
MOT_MS3: U1.43 (PE12); also elsewhere on the board
MOT_X_DIR: U1.3 (PE4); also elsewhere on the board
MOT_X_EN: U1.5 (PE6); also elsewhere on the board
MOT_X_STEP: U1.4 (PE5); also elsewhere on the board
MOT_Y0_DIR: U1.98 (PE1); also elsewhere on the board
MOT_Y0_EN: U1.2 (PE3); also elsewhere on the board
MOT_Y0_STEP: U1.1 (PE2); also elsewhere on the board
MOT_Y1_DIR: U1.95 (PB8); also elsewhere on the board
MOT_Y1_EN: U1.97 (PE0); also elsewhere on the board
MOT_Y1_STEP: U1.96 (PB9); also elsewhere on the board
MOT_Z_DIR: U1.88 (PD7); also elsewhere on the board
MOT_Z_EN: U1.91 (PB5); also elsewhere on the board
MOT_Z_STEP: U1.90 (PB4); also elsewhere on the board
unnamed: R30.1, U1.94 (BOOT0)
unnamed: C1.P$1 (1), C43.1, U1.48 (VCAP_1), U1.73 (VCAP_2)
unnamed: D4.2, R46.2
unnamed: D12.2, R47.2
unnamed: D17.2, R48.2
unnamed: D18.2, R49.2
unnamed: D18.1, U1.53 (PB14)
unnamed: D17.1, U1.52 (PB13)
unnamed: C30.1, U1.12 (PH0-OSC_IN), Y1.3
unnamed: C31.1, U1.13 (PH1), Y1.1
unnamed: D12.1, U1.37 (PB2)
unnamed: D4.1, U1.36 (PB1)
unnamed: D19.2, R50.2
unnamed: D20.2, R51.2
NRST: C29.1, R29.2, S1.1A (1), S1.1B (2), U1.14 (NRST), X21.P$3
OUTPUT_LED_BOT_UP: U1.61 (PD14); also elsewhere on the board
OUTPUT_LED_TOP_DN: U1.60 (PD13); also elsewhere on the board
OUTPUT_LED_TRAY_1: U1.59 (PD12); also elsewhere on the board
OUTPUT_LED_TRAY_2: U1.58 (PD11); also elsewhere on the board
OUTPUT_PUMP: U1.63 (PC6); also elsewhere on the board
OUTPUT_VALVE: U1.62 (PD15); also elsewhere on the board
PA0/ADC0: U1.23 (PA0), X27.P$1
PA1/ADC1: U1.24 (PA1), X27.P$2
PA2/ADC2: U1.25 (PA2), X27.P$3
PA3/ADC3: U1.26 (PA3), X27.P$4
PA4: U1.29 (PA4), X28.P$1
PA5/SPI1_SCK: U1.30 (PA5), X26.P$2
PA6/SPI1_MISO: U1.31 (PA6), X26.P$3
PA7/SPI1_MOSI: U1.32 (PA7), X26.P$4
PB0: U1.35 (PB0), X28.P$4
PB6/I2C1_SCL: R16.2, U1.92 (PB6), X19.P$1, X20.P$1
PB7/I2C1_SDA: R31.2, U1.93 (PB7), X19.P$2, X20.P$2
PB12/BUSY: R32.2, U1.51 (PB12), X19.P$3, X20.P$3
PC4: U1.33 (PC4), X28.P$2
PC5: U1.34 (PC5), X28.P$3
RX: R50.1, U1.69 (PA10); also elsewhere on the board
SYS_JTC: U1.76 (PA14), X21.P$2
SYS_JTMS-SWDIO: U1.72 (PA13), X21.P$1
TX: R51.1, U1.68 (PA9); also elsewhere on the board

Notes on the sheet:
General Purpose IO/ADC
General Purpose IO/SPI
Programmer Debugger
General Purpose IO

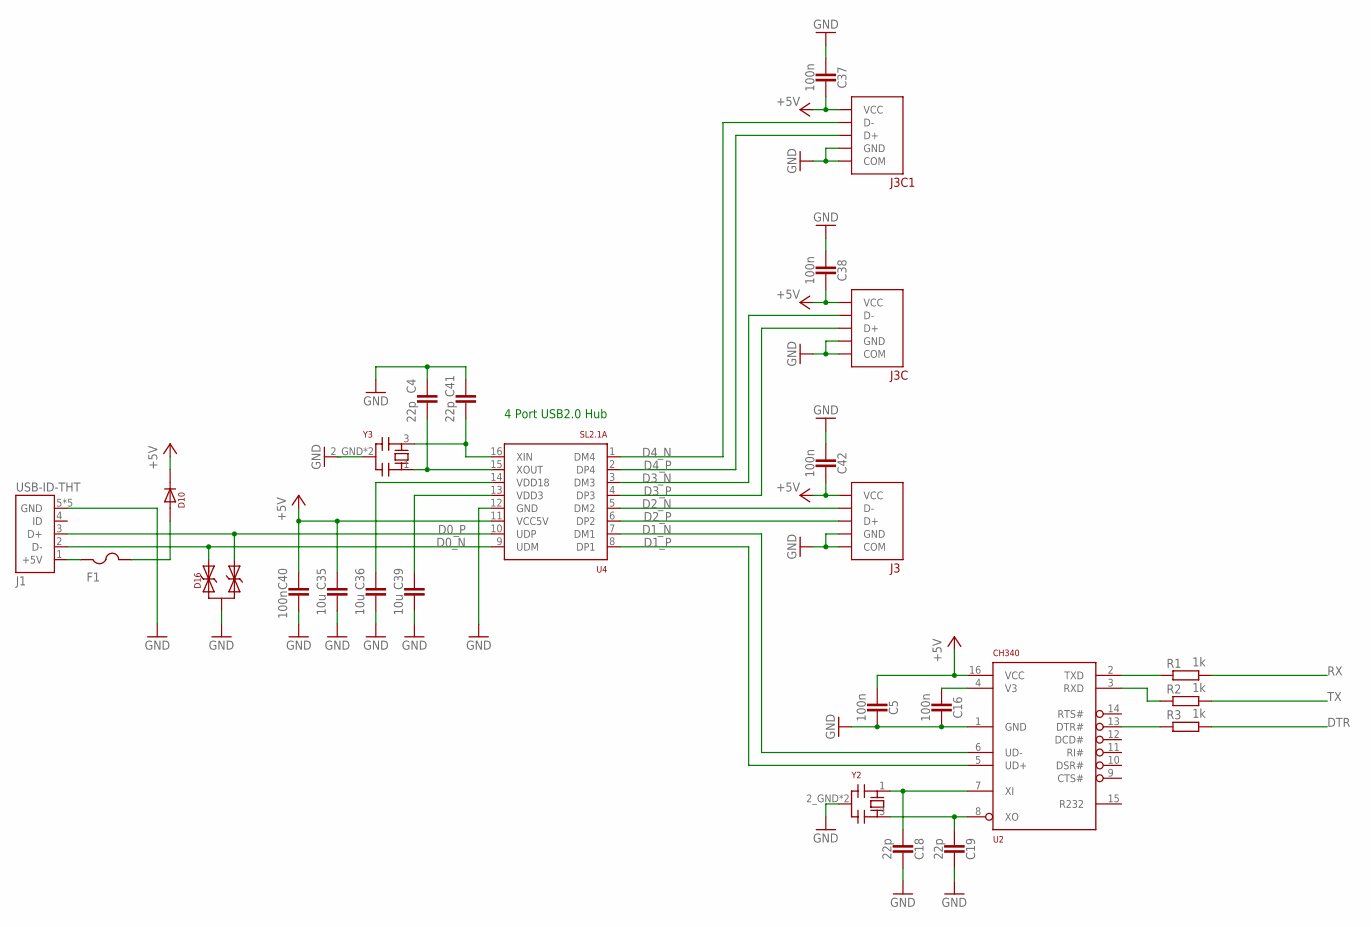
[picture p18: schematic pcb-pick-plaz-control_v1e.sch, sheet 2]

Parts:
C4, C18, C19, C41: 22p; 0603_CAP
C5, C16, C37, C38, C40, C42: 100n; 0603_CAP
C35, C36, C39: 10u; 0805_CAP
D10: DIODE-1206; 1206-DOT
D16: DIODE-TVS; SOT-23
F1: PTCFUSE-1206; R1206
J1: USB-ID-THT; USB-MICRO-THT
J3, J3C, J3C1: USB-LCSC_C42431; USB-A-LCSC_C42431
R1, R2, R3: 1k; 0603-RES
U2: CH340; SOIC-16
U4: SL2.1A; SOIC-16
Y2, Y3: 3213-QUARZ3225; 3225-QUARZ

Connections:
+5V: C5.2, C35.P$2 (2), C37.1, C38.1, C40.2, C42.1, D10.2, J3.VCC, J3C.VCC, J3C1.VCC, U2.16 (VCC), U4.11 (VCC5V); also elsewhere on the board
D0_N: D16.2, J1.2 (D-), U4.9 (UDM)
D0_P: D16.1, J1.3 (D+), U4.10 (UDP)
D1_N: U2.6 (UD-), U4.7 (DM1)
D1_P: U2.5 (UD+), U4.8 (DP1)
D2_N: J3.D-, U4.5 (DM2)
D2_P: J3.D+, U4.6 (DP2)
D3_N: J3C.D-, U4.3 (DM3)
D3_P: J3C.D+, U4.4 (DP3)
D4_N: J3C1.D-, U4.1 (DM4)
D4_P: J3C1.D+, U4.2 (DP4)
DTR: R3.2; also elsewhere on the board
GND: C4.2, C5.1, C16.1, C18.1, C19.1, C35.P$1 (1), C36.P$1 (1), C37.2, C38.2, C39.P$1 (1), C40.1, C41.2, C42.2, D16.3, J1.5 (GND), J1.GND1 (GND), J1.GND2 (GND), J1.GND3 (GND), J1.GND4 (GND), J3.COM1 (COM), J3.COM2 (COM), J3.GND, J3C.COM1 (COM), J3C.COM2 (COM), J3C.GND, J3C1.COM1 (COM), J3C1.COM2 (COM), J3C1.GND, U2.1 (GND), U4.12 (GND), Y2.2_GND (2), Y2.4_GND (2), Y3.2_GND (2), Y3.4_GND (2); also elsewhere on the board
unnamed: C18.2, U2.7 (XI), Y2.1
unnamed: C19.2, U2.8 (XO), Y2.3
unnamed: R1.1, U2.2 (TXD)
unnamed: R2.1, U2.3 (RXD)
unnamed: C16.2, U2.4 (V3)
unnamed: C41.1, U4.16 (XIN), Y3.3
unnamed: R3.1, U2.13 (DTR#)
unnamed: C4.1, U4.15 (XOUT), Y3.1
unnamed: C36.P$2 (2), U4.14 (VDD18)
unnamed: C39.P$2 (2), U4.13 (VDD3)
unnamed: D10.1, F1.2
RX: R1.2; also elsewhere on the board
TX: R2.2; also elsewhere on the board
VINUSB: F1.1, J1.1 (+5V)

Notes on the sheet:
4 Port USB2.0 Hub

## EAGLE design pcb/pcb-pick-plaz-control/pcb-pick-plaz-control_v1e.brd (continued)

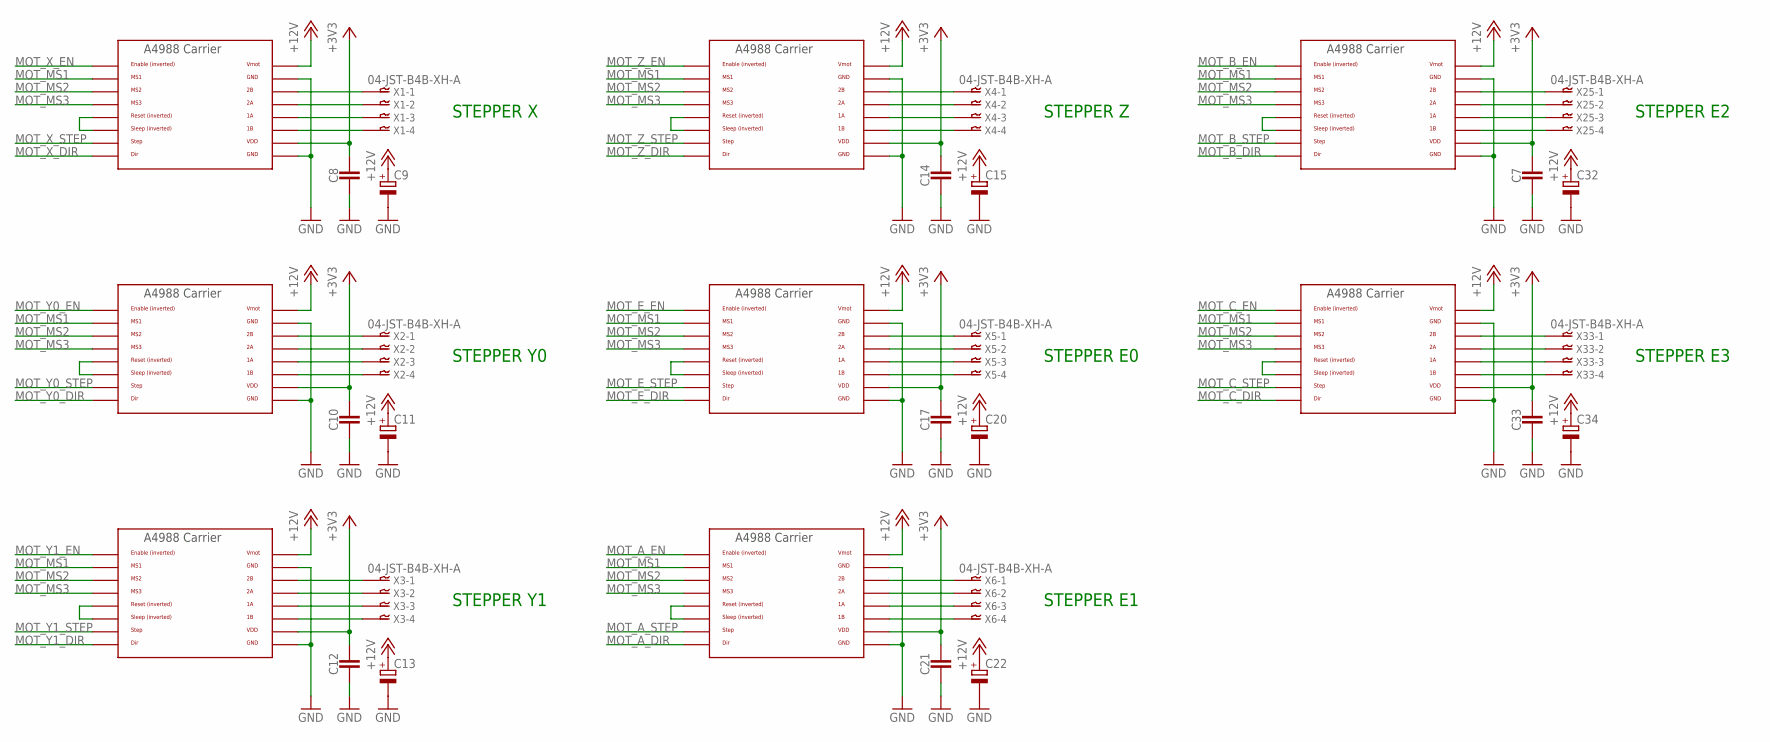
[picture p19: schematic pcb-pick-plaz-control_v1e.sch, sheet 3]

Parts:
C7, C8, C10, C12, C14, C17, C21, C33: CAPACITOR0603_CAP; 0603_CAP
C9, C11, C13, C15, C20, C22, C32, C34: CPOL-EU175TMP-0808; 175TMP-0808
U$2, U$3, U$4, U$5, U$6, U$7, U$8, U$9: A4988BREAKOUT
X1, X2, X3, X4, X5, X6, X25, X33: 04-JST-B4B-XH-A; B4B-XH

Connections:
+3V3: C7.1, C8.1, C10.1, C12.1, C14.1, C17.1, C21.1, C33.1, U$2.VDD, U$3.VDD, U$4.VDD, U$5.VDD, U$6.VDD, U$7.VDD, U$8.VDD, U$9.VDD; also elsewhere on the board
+12V: C9.+, C11.+, C13.+, C15.+, C20.+, C22.+, C32.+, C34.+, U$2.VMOT, U$3.VMOT, U$4.VMOT, U$5.VMOT, U$6.VMOT, U$7.VMOT, U$8.VMOT, U$9.VMOT; also elsewhere on the board
GND: C7.2, C8.2, C9.-, C10.2, C11.-, C12.2, C13.-, C14.2, C15.-, C17.2, C20.-, C21.2, C22.-, C32.-, C33.2, C34.-, U$2.GND, U$2.GND@0 (GND), U$3.GND, U$3.GND@0 (GND), U$4.GND, U$4.GND@0 (GND), U$5.GND, U$5.GND@0 (GND), U$6.GND, U$6.GND@0 (GND), U$7.GND, U$7.GND@0 (GND), U$8.GND, U$8.GND@0 (GND), U$9.GND, U$9.GND@0 (GND); also elsewhere on the board
MOT_A_DIR: U$7.DIR; also elsewhere on the board
MOT_A_EN: U$7.EN; also elsewhere on the board
MOT_A_STEP: U$7.STEP; also elsewhere on the board
MOT_B_DIR: U$8.DIR; also elsewhere on the board
MOT_B_EN: U$8.EN; also elsewhere on the board
MOT_B_STEP: U$8.STEP; also elsewhere on the board
MOT_C_DIR: U$9.DIR; also elsewhere on the board
MOT_C_EN: U$9.EN; also elsewhere on the board
MOT_C_STEP: U$9.STEP; also elsewhere on the board
MOT_E_DIR: U$6.DIR; also elsewhere on the board
MOT_E_EN: U$6.EN; also elsewhere on the board
MOT_E_STEP: U$6.STEP; also elsewhere on the board
MOT_MS1: U$2.MS1, U$3.MS1, U$4.MS1, U$5.MS1, U$6.MS1, U$7.MS1, U$8.MS1, U$9.MS1; also elsewhere on the board
MOT_MS2: U$2.MS2, U$3.MS2, U$4.MS2, U$5.MS2, U$6.MS2, U$7.MS2, U$8.MS2, U$9.MS2; also elsewhere on the board
MOT_MS3: U$2.MS3, U$3.MS3, U$4.MS3, U$5.MS3, U$6.MS3, U$7.MS3, U$8.MS3, U$9.MS3; also elsewhere on the board
MOT_X_DIR: U$2.DIR; also elsewhere on the board
MOT_X_EN: U$2.EN; also elsewhere on the board
MOT_X_STEP: U$2.STEP; also elsewhere on the board
MOT_Y0_DIR: U$3.DIR; also elsewhere on the board
MOT_Y0_EN: U$3.EN; also elsewhere on the board
MOT_Y0_STEP: U$3.STEP; also elsewhere on the board
MOT_Y1_DIR: U$4.DIR; also elsewhere on the board
MOT_Y1_EN: U$4.EN; also elsewhere on the board
MOT_Y1_STEP: U$4.STEP; also elsewhere on the board
MOT_Z_DIR: U$5.DIR; also elsewhere on the board
MOT_Z_EN: U$5.EN; also elsewhere on the board
MOT_Z_STEP: U$5.STEP; also elsewhere on the board
unnamed: U$2.2B, X1.P$1
unnamed: U$2.2A, X1.P$2
unnamed: U$2.1A, X1.P$3
unnamed: U$2.1B, X1.P$4
unnamed: U$6.2B, X5.P$1
unnamed: U$2.RST, U$2.SLP (SLEEP)
unnamed: U$6.2A, X5.P$2
unnamed: U$6.1A, X5.P$3
unnamed: U$3.2B, X2.P$1
unnamed: U$3.2A, X2.P$2
unnamed: U$3.1A, X2.P$3
unnamed: U$3.1B, X2.P$4
unnamed: U$3.RST, U$3.SLP (SLEEP)
unnamed: U$4.2B, X3.P$1
unnamed: U$4.2A, X3.P$2
unnamed: U$4.1A, X3.P$3
unnamed: U$4.1B, X3.P$4
unnamed: U$4.RST, U$4.SLP (SLEEP)
unnamed: U$5.2B, X4.P$1
unnamed: U$5.2A, X4.P$2
unnamed: U$5.1A, X4.P$3
unnamed: U$5.1B, X4.P$4
unnamed: U$5.RST, U$5.SLP (SLEEP)
unnamed: U$6.1B, X5.P$4
unnamed: U$6.RST, U$6.SLP (SLEEP)
unnamed: U$7.2B, X6.P$1
unnamed: U$7.2A, X6.P$2
unnamed: U$7.1A, X6.P$3
unnamed: U$7.1B, X6.P$4
unnamed: U$7.RST, U$7.SLP (SLEEP)
unnamed: U$8.2B, X25.P$1
unnamed: U$8.2A, X25.P$2
unnamed: U$8.1A, X25.P$3
unnamed: U$8.1B, X25.P$4
unnamed: U$8.RST, U$8.SLP (SLEEP)
unnamed: U$9.2B, X33.P$1
unnamed: U$9.2A, X33.P$2
unnamed: U$9.1A, X33.P$3
unnamed: U$9.1B, X33.P$4
unnamed: U$9.RST, U$9.SLP (SLEEP)

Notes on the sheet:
STEPPER X
STEPPER Y0
STEPPER Y1
STEPPER Z
STEPPER E0
STEPPER E1
STEPPER E2
STEPPER E3

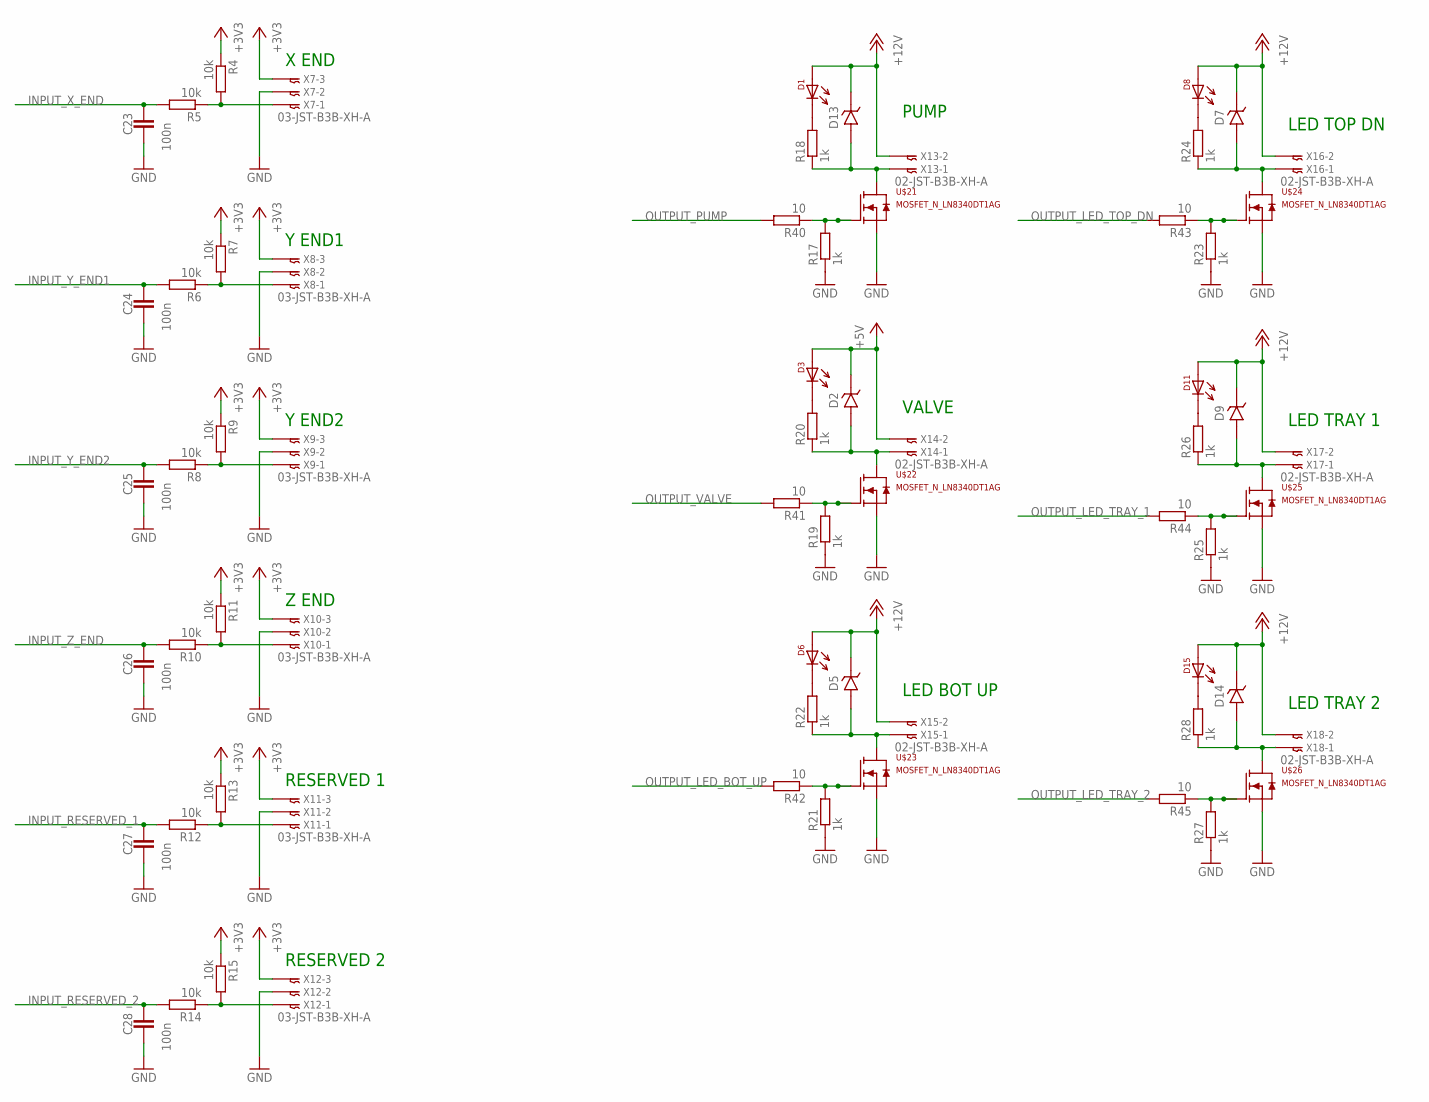
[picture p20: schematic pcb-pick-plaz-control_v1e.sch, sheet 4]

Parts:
C23, C24, C25, C26, C27, C28: 100n; 0603_CAP
D1, D3, D6, D8, D11, D15: LED-0805; 0805-DOT
D2, D5, D7, D9, D13, D14: DIODE_ZENERSOD123; SOD123
R4, R5, R6, R7, R8, R9, R10, R11, R12, R13, R14, R15: 10k; 0603-RES
R17, R18, R19, R20, R21, R22, R23, R24, R25, R26, R27, R28: 1k; 0603-RES
R40, R41, R42, R43, R44, R45: 10; 0603-RES
U$21, U$22, U$23, U$24, U$25, U$26: MOSFET_N_LN8340DT1AG; DFN3030-8B
X7, X8, X9, X10, X11, X12: 03-JST-B3B-XH-A; B3B-XH
X13, X14, X15, X16, X17, X18: 02-JST-B3B-XH-A; B2B-XH

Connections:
+3V3: R4.1, R7.1, R9.1, R11.1, R13.1, R15.1, X7.P$3, X8.P$3, X9.P$3, X10.P$3, X11.P$3, X12.P$3; also elsewhere on the board
+5V: D2.K (CATHODE), D3.1, X14.P$2; also elsewhere on the board
+12V: D1.1, D5.K (CATHODE), D6.1, D7.K (CATHODE), D8.1, D9.K (CATHODE), D11.1, D13.K (CATHODE), D14.K (CATHODE), D15.1, X13.P$2, X15.P$2, X16.P$2, X17.P$2, X18.P$2; also elsewhere on the board
GND: C23.2, C24.2, C25.2, C26.2, C27.2, C28.2, R17.1, R19.1, R21.1, R23.1, R25.1, R27.1, U$21.S1 (S), U$21.S2 (S), U$21.S3 (S), U$22.S1 (S), U$22.S2 (S), U$22.S3 (S), U$23.S1 (S), U$23.S2 (S), U$23.S3 (S), U$24.S1 (S), U$24.S2 (S), U$24.S3 (S), U$25.S1 (S), U$25.S2 (S), U$25.S3 (S), U$26.S1 (S), U$26.S2 (S), U$26.S3 (S), X7.P$2, X8.P$2, X9.P$2, X10.P$2, X11.P$2, X12.P$2; also elsewhere on the board
INPUT_RESERVED_1: C27.1, R12.2; also elsewhere on the board
INPUT_RESERVED_2: C28.1, R14.2; also elsewhere on the board
INPUT_X_END: C23.1, R5.2; also elsewhere on the board
INPUT_Y_END1: C24.1, R6.2; also elsewhere on the board
INPUT_Y_END2: C25.1, R8.2; also elsewhere on the board
INPUT_Z_END: C26.1, R10.2; also elsewhere on the board
unnamed: R4.2, R5.1, X7.P$1
unnamed: R6.1, R7.2, X8.P$1
unnamed: R8.1, R9.2, X9.P$1
unnamed: R10.1, R11.2, X10.P$1
unnamed: R12.1, R13.2, X11.P$1
unnamed: R14.1, R15.2, X12.P$1
unnamed: D13.A (ANODE), R18.1, U$21.D, X13.P$1
unnamed: R17.2, R40.1, U$21.G
unnamed: D1.2, R18.2
unnamed: D2.A (ANODE), R20.1, U$22.D, X14.P$1
unnamed: R19.2, R41.1, U$22.G
unnamed: D3.2, R20.2
unnamed: D5.A (ANODE), R22.1, U$23.D, X15.P$1
unnamed: R21.2, R42.1, U$23.G
unnamed: D6.2, R22.2
unnamed: D7.A (ANODE), R24.1, U$24.D, X16.P$1
unnamed: R23.2, R43.1, U$24.G
unnamed: D8.2, R24.2
unnamed: D9.A (ANODE), R26.1, U$25.D, X17.P$1
unnamed: R25.2, R44.1, U$25.G
unnamed: D11.2, R26.2
unnamed: D14.A (ANODE), R28.1, U$26.D, X18.P$1
unnamed: R27.2, R45.1, U$26.G
unnamed: D15.2, R28.2
OUTPUT_LED_BOT_UP: R42.2; also elsewhere on the board
OUTPUT_LED_TOP_DN: R43.2; also elsewhere on the board
OUTPUT_LED_TRAY_1: R44.2; also elsewhere on the board
OUTPUT_LED_TRAY_2: R45.2; also elsewhere on the board
OUTPUT_PUMP: R40.2; also elsewhere on the board
OUTPUT_VALVE: R41.2; also elsewhere on the board

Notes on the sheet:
PUMP
VALVE
LED BOT UP
LED TOP DN
LED TRAY 1
LED TRAY 2
X END
Y END1
Y END2
Z END
RESERVED 1
RESERVED 2

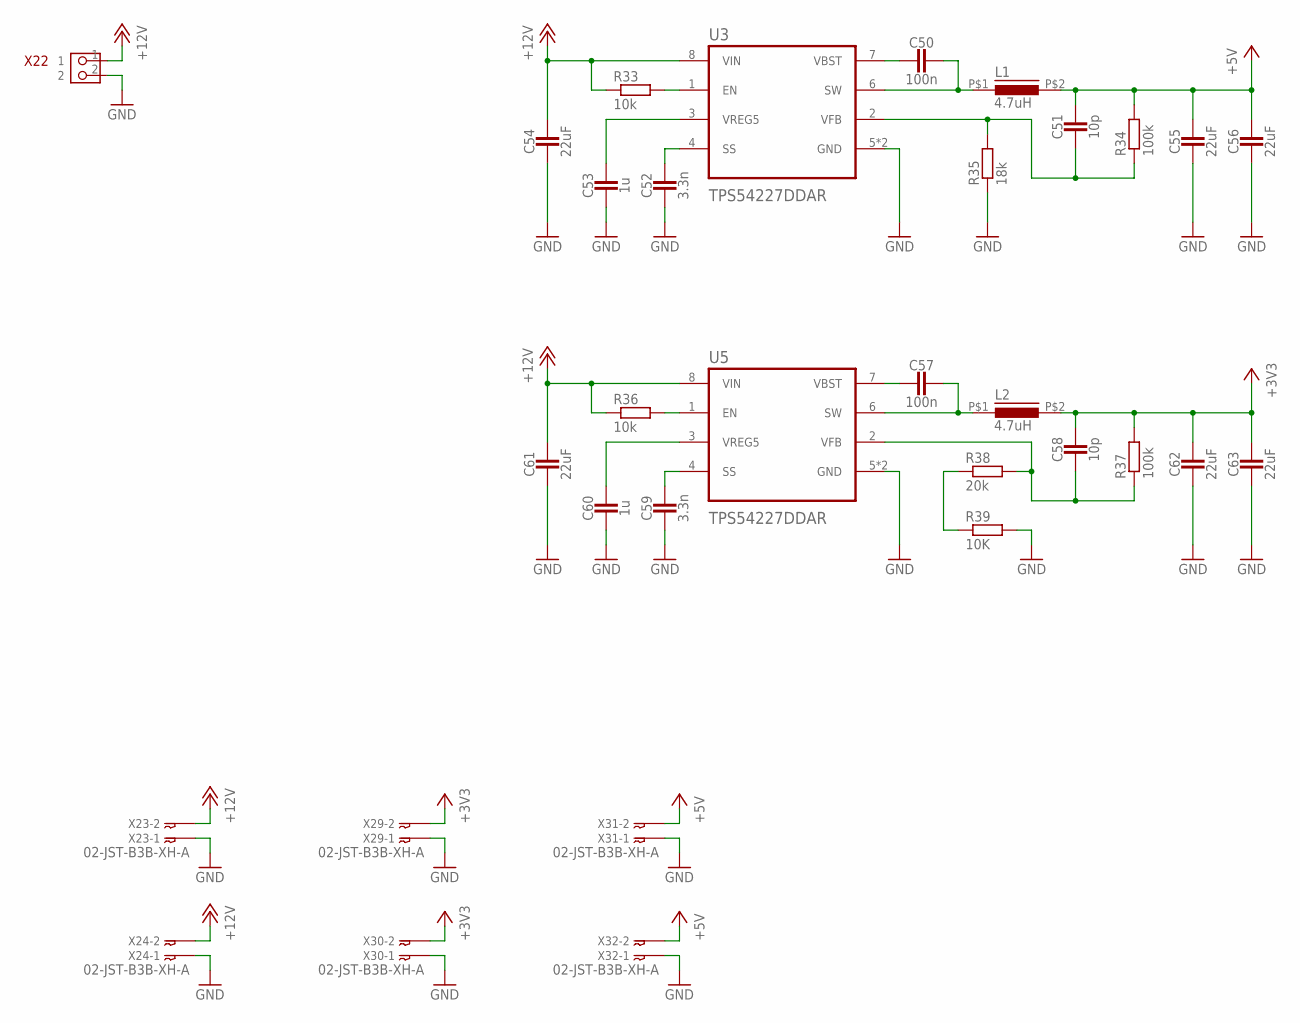
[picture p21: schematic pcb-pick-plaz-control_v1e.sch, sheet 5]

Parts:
C50, C57: 100n; 0603_CAP
C51, C58: 10p; 0603_CAP
C52, C59: 3.3n; 0603_CAP
C53, C60: 1u; 0603_CAP
C54, C61: 22uF; 1206_CAP
C55, C56, C62, C63: 22uF; 0805_CAP
L1, L2: 4.7uH; IND_CR4
R33, R36: 10k; 0603-RES
R34, R37: 100k; 0603-RES
R35: 18k; 0603-RES
R38: 20k; 0603-RES
R39: 10K; 0603-RES
U3, U5: TPS54227DDAR; TPS54227DDAR_VREG_LM5017MR/NOPB
X22: PIN_2X13.81MM_LONGPAD; PIN_2X1_3.81MM_LONGPAD
X23, X24, X29, X30, X31, X32: 02-JST-B3B-XH-A; B2B-XH

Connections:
+3V3: C58.1, C62.P$1 (1), C63.P$1 (1), L2.P$2 (2), R37.2, X29.P$2, X30.P$2; also elsewhere on the board
+5V: C51.1, C55.P$1 (1), C56.P$1 (1), L1.P$2 (2), R34.2, X31.P$2, X32.P$2; also elsewhere on the board
+12V: C54.1, C61.1, R33.1, R36.1, U3.8 (VIN), U5.8 (VIN), X22.1, X23.P$2, X24.P$2; also elsewhere on the board
GND: C52.2, C53.2, C54.2, C55.P$2 (2), C56.P$2 (2), C59.2, C60.2, C61.2, C62.P$2 (2), C63.P$2 (2), R35.1, R39.2, U3.5 (GND), U3.9 (GND), U5.5 (GND), U5.9 (GND), X22.2, X23.P$1, X24.P$1, X29.P$1, X30.P$1, X31.P$1, X32.P$1; also elsewhere on the board
unnamed: C50.2, U3.7 (VBST)
unnamed: C50.1, L1.P$1 (1), U3.6 (SW)
unnamed: C51.2, R34.1, R35.2, U3.2 (VFB)
unnamed: C52.1, U3.4 (SS)
unnamed: C53.1, U3.3 (VREG5)
unnamed: R33.2, U3.1 (EN)
unnamed: C57.2, U5.7 (VBST)
unnamed: C57.1, L2.P$1 (1), U5.6 (SW)
unnamed: C58.2, R37.1, R38.2, U5.2 (VFB)
unnamed: C59.1, U5.4 (SS)
unnamed: C60.1, U5.3 (VREG5)
unnamed: R36.2, U5.1 (EN)
unnamed: R38.1, R39.1


Board: 4 copper layers, 100.0 x 100.0 mm, 202 parts (0 on the bottom side), 176 nets.

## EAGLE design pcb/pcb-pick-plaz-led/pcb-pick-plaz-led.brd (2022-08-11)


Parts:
D1, D2, D3, D4, D5, D6, D7, D8, D9, D10, D11, D12, D13, D14, D15, D16, D17, D18, D19, D20, D21, D22, D23, D24, D25, D26, D27, D28, D29, D30, D31, D32, D33, D34, D35, D36, D37, D38, D39, D40, D41, D42, D43, D44, D45, D46, D47, D48: LED-5730; 5730-LED
R1, R2, R3, R4, R5, R6, R7, R8, R9, R10, R11, R12, R13, R14, R15, R16: 470; 0805_RES
U$1: LOGO-TOBENG-1MM-FINISH; TOBENG-1MM-FINISH
U$2, U$3: 02-JST-B3B-XH-A; B2B-XH
V1, V2, V3, V4: FIDUCIAL2MM; FIDUCIAL_2MM

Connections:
GND: R1.1, R2.1, R3.1, R4.1, R5.1, R6.1, R7.1, R8.1, R9.1, R10.1, R11.1, R12.1, R13.1, R14.1, R15.1, R16.1, U$2.P$2, U$3.P$2
unnamed: D1.C (2), D2.A1 (1), D2.A2 (1)
unnamed: D2.C (2), D3.A1 (1), D3.A2 (1)
unnamed: D3.C (2), R1.2
unnamed: D4.C (2), D5.A1 (1), D5.A2 (1)
unnamed: D5.C (2), D6.A1 (1), D6.A2 (1)
unnamed: D6.C (2), R2.2
unnamed: D7.C (2), D8.A1 (1), D8.A2 (1)
unnamed: D8.C (2), D9.A1 (1), D9.A2 (1)
unnamed: D9.C (2), R3.2
unnamed: D10.C (2), D11.A1 (1), D11.A2 (1)
unnamed: D11.C (2), D12.A1 (1), D12.A2 (1)
unnamed: D12.C (2), R4.2
unnamed: D13.C (2), D14.A1 (1), D14.A2 (1)
unnamed: D14.C (2), D15.A1 (1), D15.A2 (1)
unnamed: D15.C (2), R5.2
unnamed: D16.C (2), D17.A1 (1), D17.A2 (1)
unnamed: D17.C (2), D18.A1 (1), D18.A2 (1)
unnamed: D18.C (2), R6.2
unnamed: D19.C (2), D20.A1 (1), D20.A2 (1)
unnamed: D20.C (2), D21.A1 (1), D21.A2 (1)
unnamed: D21.C (2), R7.2
unnamed: D22.C (2), D23.A1 (1), D23.A2 (1)
unnamed: D23.C (2), D24.A1 (1), D24.A2 (1)
unnamed: D24.C (2), R8.2
unnamed: D25.C (2), D26.A1 (1), D26.A2 (1)
unnamed: D26.C (2), D27.A1 (1), D27.A2 (1)
unnamed: D27.C (2), R9.2
unnamed: D28.C (2), D29.A1 (1), D29.A2 (1)
unnamed: D29.C (2), D30.A1 (1), D30.A2 (1)
unnamed: D30.C (2), R10.2
unnamed: D31.C (2), D32.A1 (1), D32.A2 (1)
unnamed: D32.C (2), D33.A1 (1), D33.A2 (1)
unnamed: D33.C (2), R11.2
unnamed: D34.C (2), D35.A1 (1), D35.A2 (1)
unnamed: D35.C (2), D36.A1 (1), D36.A2 (1)
unnamed: D36.C (2), R12.2
unnamed: D37.C (2), D38.A1 (1), D38.A2 (1)
unnamed: D38.C (2), D39.A1 (1), D39.A2 (1)
unnamed: D39.C (2), R13.2
unnamed: D40.C (2), D41.A1 (1), D41.A2 (1)
unnamed: D41.C (2), D42.A1 (1), D42.A2 (1)
unnamed: D42.C (2), R14.2
unnamed: D43.C (2), D44.A1 (1), D44.A2 (1)
unnamed: D44.C (2), D45.A1 (1), D45.A2 (1)
unnamed: D45.C (2), R15.2
unnamed: D46.C (2), D47.A1 (1), D47.A2 (1)
unnamed: D47.C (2), D48.A1 (1), D48.A2 (1)
unnamed: D48.C (2), R16.2
VCC: D1.A1 (1), D1.A2 (1), D4.A1 (1), D4.A2 (1), D7.A1 (1), D7.A2 (1), D10.A1 (1), D10.A2 (1), D13.A1 (1), D13.A2 (1), D16.A1 (1), D16.A2 (1), D19.A1 (1), D19.A2 (1), D22.A1 (1), D22.A2 (1), D25.A1 (1), D25.A2 (1), D28.A1 (1), D28.A2 (1), D31.A1 (1), D31.A2 (1), D34.A1 (1), D34.A2 (1), D37.A1 (1), D37.A2 (1), D40.A1 (1), D40.A2 (1), D43.A1 (1), D43.A2 (1), D46.A1 (1), D46.A2 (1), U$2.P$1, U$3.P$1



Board: 2 copper layers, 100.0 x 100.0 mm, 71 parts (2 on the bottom side), 50 nets.

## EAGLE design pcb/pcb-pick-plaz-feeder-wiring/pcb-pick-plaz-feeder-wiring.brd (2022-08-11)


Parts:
D1, D2, D3, D15: LED-0805; 0805-DOT
J1, J2, J3, J4: 03-JST-B3B-XH-A; B3B-XH
J5: 02-JST-B3B-XH-A; B2B-XH
J6: 05-JST-B5B-XH-A; B5B-XH
R1, R2, R3, R9: 1k; 0603-RES
U$1: LOGO-TOBENG-1MM-FINISH; TOBENG-1MM-FINISH

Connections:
+5V: J1.P$3, J2.P$3, J3.P$3, J4.P$3, J5.P$2
GND: D1.2, D2.2, D3.2, D15.2, J1.P$1, J2.P$1, J3.P$1, J4.P$1, J5.P$1, J6.P$5
unnamed: J3.P$2, J6.P$3, R1.1
unnamed: J4.P$2, J6.P$4, R9.1
unnamed: D1.1, R1.2
unnamed: J2.P$2, J6.P$2, R2.1
unnamed: J1.P$2, J6.P$1, R3.1
unnamed: D15.1, R9.2
unnamed: D2.1, R2.2
unnamed: D3.1, R3.2


Board: 2 copper layers, 40.0 x 60.0 mm, 15 parts (0 on the bottom side), 10 nets.

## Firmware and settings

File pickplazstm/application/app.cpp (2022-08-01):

/*
 * app.cpp
 *
 *  Created on: May 29, 2021
 *      Author: ftobler
 */


#include "app.h"
#include "stdint.h"
#include "arduino_like_hal.h"
#include "AccelStepperExtended.h"
#include "uart_handler.h"
#include "io.h"
#include "cmsis_gcc.h"


static void default_settings();
static bool is_steppers_on_position();
static void do_cmd_drive_to_position(Gcode_command cmd);
static void do_cmd_home(Gcode_command cmd);
static void homeAxle(AccelStepperExtended* stepper, Prelling_input* endstop, int homDirection, float home_speed = 10.0f, int home_timeout = 10000,
		float home_travel_mm = 1000.0f, float home_travel_back_mm = 5.0f, float sensor_position = -1.0f);
static void homeAxleDual(AccelStepperExtended* stepper1, AccelStepperExtended* stepper2, Prelling_input* endstop1, Prelling_input* endstop2,
		int homDirection, float home_speed = 10.0f, int home_timeout = 10000, float home_travel_mm = 1000.0f, float home_travel_back_mm = 5.0f, float sensor_position = -1.0f);
static void do_cmd_dwell(Gcode_command cmd);
static void do_cmd_set_position(Gcode_command cmd);
static void do_cmd_vacuum_pump(bool on);
static void do_cmd_vacuum_valve(bool on);
static void do_cmd_io(Gcode_command cmd);
static void do_cmd_stepper_power(bool on);
static void do_cmd_set_max_acceleration(Gcode_command cmd);
static void do_cmd_set_max_speed(Gcode_command cmd);
static void do_cmd_set_max_speed_multiplier(Gcode_command cmd);
static void do_cmd_feeder(Gcode_command cmd);
static void job_prelling_handle();


//output pin cluster (these have FET driver to either 5V or 12V)
#define PIN_OUTPUT_PUMP  portpin('C', 6)  //12V
#define PIN_OUTPUT_AUX1  portpin('D', 15) //written as VALVE on PCB on early revision. 5V
#define PIN_OUTPUT_FAN   portpin('D', 14) //written as BOTUP on PCB. 12V
#define PIN_OUTPUT_TOPDN portpin('D', 13) //12V
#define PIN_OUTPUT_VALVE portpin('D', 12) //written as AUX1 on PCB on early revision. 12V
#define PIN_OUTPUT_TRAY  portpin('D', 11) //written as AUX2 on PCB on early revision. 12V

//Input pin cluster
#define PIN_INPUT_XEND  portpin('D', 10)
#define PIN_INPUT_YEND0 portpin('D', 9)
#define PIN_INPUT_YEND1 portpin('D', 8)
#define PIN_INPUT_ZEND  portpin('E', 15)
#define PIN_INPUT_RES1  portpin('E', 14)
#define PIN_INPUT_RES2  portpin('E', 13)

//Stepper Motor Drivers
#define PIN_MOTX_STEP  portpin('E', 5)
#define PIN_MOTX_DIR   portpin('E', 4)
#define PIN_MOTX_EN    portpin('E', 6)

#define PIN_MOTY0_STEP portpin('E', 2)
#define PIN_MOTY0_DIR  portpin('E', 1)
#define PIN_MOTY0_EN   portpin('E', 3)

#define PIN_MOTY1_STEP portpin('B', 9)
#define PIN_MOTY1_DIR  portpin('B', 8)
#define PIN_MOTY1_EN   portpin('E', 0)

#define PIN_MOTZ_STEP  portpin('B', 4)
#define PIN_MOTZ_DIR   portpin('D', 7)
#define PIN_MOTZ_EN    portpin('B', 5)

#define PIN_MOTE_STEP  portpin('D', 5)
#define PIN_MOTE_DIR   portpin('D', 4)
#define PIN_MOTE_EN    portpin('D', 6)

#define PIN_MOTA_STEP  portpin('D', 2)
#define PIN_MOTA_DIR   portpin('D', 1)
#define PIN_MOTA_EN    portpin('D', 6)

#define PIN_MOTB_STEP  portpin('C', 8)
#define PIN_MOTB_DIR   portpin('C', 7)
#define PIN_MOTB_EN    portpin('C', 9)

#define PIN_MOTC_STEP  portpin('C', 12)
#define PIN_MOTC_DIR   portpin('C', 11)
#define PIN_MOTC_EN    portpin('D', 0)

//debug leds
#define PIN_DEBUG0     portpin('B', 1)
#define PIN_DEBUG1     portpin('B', 2)
#define PIN_DEBUG2     portpin('B', 13)
#define PIN_DEBUG3     portpin('B', 14)

//microstep setting
#define PIN_MOT_MS1    portpin('E', 10)
#define PIN_MOT_MS2    portpin('E', 11)
#define PIN_MOT_MS3    portpin('E', 12)

//feeder pins
#define PIN_FEEDER0    portpin('A', 4)
#define PIN_FEEDER1    portpin('C', 4)
#define PIN_FEEDER2    portpin('C', 5)
#define PIN_FEEDER3    portpin('B', 0)

//Steper Motor instances
AccelStepperExtended stepperX( PIN_MOTX_STEP,  PIN_MOTX_DIR);
AccelStepperExtended stepperY0(PIN_MOTY0_STEP, PIN_MOTY0_DIR);
AccelStepperExtended stepperY1(PIN_MOTY1_STEP, PIN_MOTY1_DIR);
AccelStepperExtended stepperZ( PIN_MOTZ_STEP,  PIN_MOTZ_DIR);
AccelStepperExtended stepperE( PIN_MOTE_STEP,  PIN_MOTE_DIR);
AccelStepperExtended stepperA( PIN_MOTA_STEP,  PIN_MOTA_DIR);
AccelStepperExtended stepperB( PIN_MOTB_STEP,  PIN_MOTB_DIR);
AccelStepperExtended stepperC( PIN_MOTC_STEP,  PIN_MOTC_DIR);

//output pin cluster
Simple_output output_pump(PIN_OUTPUT_PUMP);
Simple_output output_aux1(PIN_OUTPUT_AUX1);
Delay_off_out output_fan(PIN_OUTPUT_FAN, 60000);
Simple_output output_topdn(PIN_OUTPUT_TOPDN);
Simple_output output_valve(PIN_OUTPUT_VALVE);
Simple_output output_tray(PIN_OUTPUT_TRAY);

//input pin cluster
Prelling_input input_endX(PIN_INPUT_XEND);
Prelling_input input_endY0(PIN_INPUT_YEND0);
Prelling_input input_endY1(PIN_INPUT_YEND1);
Prelling_input input_endZ(PIN_INPUT_ZEND);
Prelling_input input_res1(PIN_INPUT_RES1);
Prelling_input input_res2(PIN_INPUT_RES2);

//feeder cluster
Feeder_automatic feeder0(PIN_FEEDER0);
Feeder_automatic feeder1(PIN_FEEDER1);
Feeder_automatic feeder2(PIN_FEEDER2);
Feeder_automatic feeder3(PIN_FEEDER3);


static bool job_prelling = false;
static float target_completeness = NaN;
static float current_speed = 175.0f;


/**
 * Program setup
 * Does run once
 */
void setup() {


	//set microstepping to 4x
	//works only on board v1e or later
	digitalWrite(PIN_MOT_MS1, 0);
	digitalWrite(PIN_MOT_MS2, 1);
	digitalWrite(PIN_MOT_MS3, 0);

	default_settings();

	uart_init();


	output_fan.set(true);
	do_cmd_stepper_power(false);
}


/*
 * apply defaultl settings on the controller
 * This is used as a revert back to normal
 */
static void default_settings() {
	float steps_per_mm =   50.0f*2.0f;
	//this is stable speed, but it seems a bit slow
	float speed_cap =     120.0f;
	float speed =         120.0f;
	float accel =         600.0f;

	//this was too fast
	// float speed_cap =     175.0f;
	// float speed =         175.0f;
	// float accel =        1000.0f;
	current_speed = speed;
	//note:
	//Trinamic drivers seem to 'wander' slowly, could have to do with
	//their interpolation and the fact that the step pin
	//might be stuck at high.

	stepperX.setStepsPer_mm(steps_per_mm);
	stepperX.setAcceleration_mm(accel);
	stepperX.setMaxSpeed_cap_mm(speed_cap);
	stepperX.setMaxSpeed_mm(speed);
	stepperX.setMaxSpeed_multiplier_mm(1.0);
//	stepperX._isTrinamic = true;

	stepperY0.setStepsPer_mm(steps_per_mm);
	stepperY0.setAcceleration_mm(accel);
	stepperY0.setMaxSpeed_cap_mm(speed_cap);
	stepperY0.setMaxSpeed_mm(speed);
	stepperY0.setMaxSpeed_multiplier_mm(1.0);

	stepperY1.setStepsPer_mm(steps_per_mm);
	stepperY1.setAcceleration_mm(accel);
	stepperY1.setMaxSpeed_cap_mm(speed_cap);
	stepperY1.setMaxSpeed_mm(speed);
	stepperY1.setMaxSpeed_multiplier_mm(1.0);

	stepperZ.setStepsPer_mm(steps_per_mm/2.0f);
	stepperZ.setAcceleration_mm(accel);
	stepperZ.setMaxSpeed_cap_mm(speed_cap*2.0f);
	stepperZ.setMaxSpeed_mm(speed*2.0f);
	stepperZ.setMaxSpeed_multiplier_mm(1.0);

	stepperE.setStepsPer_mm(2.222222f*2.0f);
	stepperE.setAcceleration_mm(15000.0f);
	stepperE.setMaxSpeed_cap_mm(2000.0f);
	stepperE.setMaxSpeed_mm(2000.0f);
	stepperE.setMaxSpeed_multiplier_mm(12.0);

	stepperA.setStepsPer_mm(steps_per_mm);
	stepperA.setAcceleration_mm(accel);
	stepperA.setMaxSpeed_cap_mm(speed_cap);
	stepperA.setMaxSpeed_mm(speed);
	stepperA.setMaxSpeed_multiplier_mm(1.0);

	stepperB.setStepsPer_mm(steps_per_mm);
	stepperB.setAcceleration_mm(accel);
	stepperB.setMaxSpeed_cap_mm(speed_cap);
	stepperB.setMaxSpeed_mm(speed);
	stepperB.setMaxSpeed_multiplier_mm(1.0);

	stepperC.setStepsPer_mm(steps_per_mm);
	stepperC.setAcceleration_mm(accel);
	stepperC.setMaxSpeed_cap_mm(speed_cap);
	stepperC.setMaxSpeed_mm(speed);
	stepperC.setMaxSpeed_multiplier_mm(1.0);
}


/**
 * Fast timer ISR. Frequency is around multiple kHz
 */
void timer_isr() {
	if (stepperX.isRunning())  stepperX.run();
	if (stepperY0.isRunning()) stepperY0.run();
	if (stepperY1.isRunning()) stepperY1.run();
	if (stepperZ.isRunning())  stepperZ.run();
	if (stepperE.isRunning())  stepperE.run();
	if (stepperA.isRunning())  stepperA.run();
	if (stepperB.isRunning())  stepperB.run();
	if (stepperC.isRunning())  stepperC.run();
}


/**
 * Slow ISR. Frquency is 1kHz
 */
void systick_isr() {
	job_prelling = true;
}


/**
 * Background loop of Microcontroller
 */
void loop() {

	uart_loop();
	if (uart_command_available() && is_steppers_on_position()) {
		Gcode_command cmd = uart_command_get();
		target_completeness = NaN; //initialize default
		if (cmd.id == 'G' && (cmd.num == 0 || cmd.num == 1)) {
			//drive to position
			//there is no difference between G0 and G1
			//Each motor drives at its own max speed. Some axies might reach the target
			//before others
			//eg:  G0 X10 Y20 => drive X to 10 and Y to 20. All other motors are not changed in position
			//axies are: X, Y, Z, E, A, B, C
			do_cmd_drive_to_position(cmd);
		} else if (cmd.id == 'G' && (cmd.num == 28)) {
			//home all axies. They are homed in an order which is safe for the machine
			//eg:  G28
			//axies which are homed are: Z, X, Y (in that order)
			do_cmd_stepper_power(true);  //switch it on first.
			do_cmd_home(cmd);
		} else if (cmd.id == 'G' && (cmd.num == 4)) {
			//dwell / wait for a given amount of time
			//eg: G4 T5.5 => wait for 5.5s
			do_cmd_dwell(cmd);
		} else if (cmd.id == 'G' && (cmd.num == 92)) {
			//set position ot the motors without driving them
			//eg:  G0 X10 Y20 => set X to 10 and Y to 20
			do_cmd_set_position(cmd);
		} else if (cmd.id == 'M' && (cmd.num == 6)) {
			//tool change command
			//not implemented
		} else if (cmd.id == 'M' && (cmd.num == 10)) {
			//vacuum pump on
			//eg: M10
			do_cmd_vacuum_pump(true);
		} else if (cmd.id == 'M' && (cmd.num == 11)) {
			//vacuum pump off
			//eg: M11
			do_cmd_vacuum_pump(false);
		} else if (cmd.id == 'M' && (cmd.num == 17)) {
			//steppers ON
			//eg: M17
			do_cmd_stepper_power(true);
		} else if (cmd.id == 'M' && (cmd.num == 18)) {
			//steppers OFF
			//eg: M18
			do_cmd_stepper_power(false);
		} else if (cmd.id == 'M' && (cmd.num == 126)) {
			//open valve (powers it)
			//eg: M126
			do_cmd_vacuum_valve(true);
		} else if (cmd.id == 'M' && (cmd.num == 127)) {
			//close valve (un-powers it)
			//eg: M127
			do_cmd_vacuum_valve(false);
		} else if (cmd.id == 'M' && (cmd.num == 42)) {
			//switch io pin
			//eg M42 P0 S1 => turns output 0 on
			//the outputs are driven by a low side FET and either 5V or 12V
			do_cmd_io(cmd);
		} else if (cmd.id == 'M' && (cmd.num == 201)) {
			//set max acceleration
			//eg: M201 X500 => sets only X-axies to 500mm/s^2
			do_cmd_set_max_acceleration(cmd);
		} else if (cmd.id == 'M' && (cmd.num == 203)) {
			//set max feedrate
			//set max acceleration
			//eg: M203 X50 => sets only X-axies to 50mm/s
			do_cmd_set_max_speed(cmd);
		} else if (cmd.id == 'M' && (cmd.num == 204)) {
			//set max feedrate multiplier
			//this factor is normally 1.0000
			//it will be applied on G0/G1 commands when the F-Parameter is given
			//the given speed is multiplied with this factor before setting it.
			//this allows slow rotating axies to kind of ignore the F-Parameter
			//eg: M204 X1.00
			do_cmd_set_max_speed_multiplier(cmd);
		} else if (cmd.id == 'M' && (cmd.num == 205)) {
			//control feeders (all of them)
			//feeder number is specified on 'P'    - P = 0..3
			//feeder direction is specified on 'S' - (S > 0.5) => forward, (s <= 0.5) => backward
			//eg: M205 P2 S1 => will advance feeder 2 to the next part
			do_cmd_feeder(cmd);
		} else if (cmd.id == 'M' && (cmd.num == 206)) {
			//system reset.
			//eg: M206
			do_cmd_stepper_power(false);
			do_cmd_vacuum_pump(false);
			do_cmd_vacuum_valve(false);
			HAL_NVIC_SystemReset();
		} else if (cmd.id == 'M' && (cmd.num == 512)) {
			//set default state for feedrate & accelerations
			//eg: M512
			default_settings();
		} else if (cmd.id == 'M' && (cmd.num == 1000)) {
			//send sync back to uart
			//use this to detect when the machine has successfully cleared the queue to this point.
			//eg: M1000
			uart_message("SYNC");
		} else {
			//unknown command
			uart_message("ERR_COMMAND_NOT_FOUND");
		}
		if (!uart_command_available()) {
			uart_message("EMPTY");
		}
	}

	job_prelling_handle();

}


static bool is_steppers_on_position() {
	if (target_completeness == NaN) {
		if (stepperX.isRunning()) return false;
		if (stepperY0.isRunning()) return false;
		if (stepperY1.isRunning()) return false;
		if (stepperZ.isRunning()) return false;
		if (stepperE.isRunning()) return false;
		if (stepperA.isRunning()) return false;
		if (stepperB.isRunning()) return false;
		if (stepperC.isRunning()) return false;
	} else {
		float complete = target_completeness; //buffer float
		if (stepperX.getRemainingMoveLength() > complete) return false;
		if (stepperY0.getRemainingMoveLength() > complete) return false;
		if (stepperY1.getRemainingMoveLength() > complete) return false;
		if (stepperZ.getRemainingMoveLength() > complete) return false;
		if (stepperE.getRemainingMoveLength() > complete) return false;
		if (stepperA.getRemainingMoveLength() > complete) return false;
		if (stepperB.getRemainingMoveLength() > complete) return false;
		if (stepperC.getRemainingMoveLength() > complete) return false;
	}
	return true;
}


static void do_cmd_drive_to_position(Gcode_command cmd) {
	if (cmd.valueF != NaN) {
		current_speed = cmd.valueF;
	}
	float speed = current_speed;
	stepperX.setMaxSpeed_mm(speed);
	stepperY0.setMaxSpeed_mm(speed);
	stepperY1.setMaxSpeed_mm(speed);
	stepperZ.setMaxSpeed_mm(speed);
	stepperE.setMaxSpeed_mm(speed);
	stepperA.setMaxSpeed_mm(speed);
	stepperB.setMaxSpeed_mm(speed);
	stepperC.setMaxSpeed_mm(speed);

	if (cmd.valueX != NaN) {
		stepperX.moveTo_mm(cmd.valueX);
	}
	if (cmd.valueY != NaN) {
		stepperY0.moveTo_mm(cmd.valueY);
		stepperY1.moveTo_mm(cmd.valueY);
	}
	if (cmd.valueZ != NaN) {
		stepperZ.moveTo_mm(cmd.valueZ);
	}
	if (cmd.valueE != NaN) {
		stepperE.moveTo_mm(cmd.valueE);
	}
	if (cmd.valueA != NaN) {
		stepperA.moveTo_mm(cmd.valueA);
	}
	if (cmd.valueB != NaN) {
		stepperB.moveTo_mm(cmd.valueB);
	}
	if (cmd.valueC != NaN) {
		stepperC.moveTo_mm(cmd.valueC);
	}
	if (cmd.valueR != NaN) {
		if (cmd.valueR < 0.0f) {
			target_completeness = 0.0f;
		} else {
			target_completeness = cmd.valueR;
		}
	}
}


static void do_cmd_home(Gcode_command cmd) {
	target_completeness = NaN; //can't have that here

	//home all axles if no extra parameters given
	if (cmd.valueX == NaN && cmd.valueX == NaN && cmd.valueZ == NaN) {
		cmd.valueX = 0;
		cmd.valueY = 0;
		cmd.valueZ = 0;
	}
	if (cmd.valueZ != NaN) {
		float tmpSpeed = stepperZ.getMaxSpeed_mm();
		       //motor      endstop     dir  speed     timeout  travel backtravel
		homeAxle(&stepperZ, &input_endZ,  1, 80.0f/4.0f, 5000,   30.0f, 7.5f, 9.0f);
		stepperZ.setMaxSpeed_mm(tmpSpeed);
	}
	if (cmd.valueX != NaN) {
		float tmpSpeed = stepperX.getMaxSpeed_mm();
	           //motor      endstop     dir  speed     timeout  travel backtravel
		homeAxle(&stepperX, &input_endX, -1, 80.0f/4.0f, 30000, 400.0f, 3.0f, -1.0f);
		stepperX.setMaxSpeed_mm(tmpSpeed);
	}
	if (cmd.valueY != NaN) {
		float tmpSpeed = stepperY0.getMaxSpeed_mm();
	                //motor1     motor2      endstop1      endstop2     dir  speed     timeout  travel backtravel
		homeAxleDual(&stepperY0, &stepperY1, &input_endY0, &input_endY1, -1, 80.0f/4.0f, 30000, 400.0f, 3.0f, -1.0f);
		stepperY0.setMaxSpeed_mm(tmpSpeed);
		stepperY1.setMaxSpeed_mm(tmpSpeed);
	}
}


static void homeAxle(AccelStepperExtended* stepper, Prelling_input* endstop, int homDirection, float home_speed, int home_timeout,
		float home_travel_mm, float home_travel_back_mm, float sensor_position) {
	uint32_t endtime;
	target_completeness = NaN; //can't have that here


	stepper->setMaxSpeed_mm(home_speed);                         //set homing fast speed for 1st travel
	stepper->setCurrentPosition_mm(0.0f);                         //reset position to 0
	stepper->moveTo_mm(home_travel_mm * homDirection);           //run to endstop
	endtime = millis() + home_timeout;
	while (endstop->get() && (millis() < endtime)) {              //block until endstop or timeout reached
		__WFI();
		job_prelling_handle();
	}
	if (millis() >= endtime) return;
	stepper->move(0);                                            //stepper shoud stop immediately
	stepper->setCurrentPosition_mm(0.0f);                         //reset position to 0
	stepper->moveTo_mm(home_travel_back_mm * homDirection * -1.0f); //go back a bit
	while (stepper->isRunning()) {                               //block until stepper reached position
		__WFI();
	    job_prelling_handle();
	}
	stepper->setMaxSpeed_mm(home_speed / 6.0f);                     //set slow speed for 2nd forward motion
	stepper->moveTo_mm(home_travel_back_mm * 2.0f * homDirection);  //move to endstop 2nd time
	endtime = millis() + home_timeout / 2.0f;
	while (endstop->get() && (millis() < endtime)) {              //block until endstop or timeout reached
		__WFI();
		job_prelling_handle();
	}
	if (millis() >= endtime) return;
	stepper->move(0);                                            //stepper shoud stop immediately
	stepper->setCurrentPosition_mm(sensor_position);                       //homing finished
	stepper->moveTo_mm(0.0f);
}


static void homeAxleDual(AccelStepperExtended* stepper1, AccelStepperExtended* stepper2, Prelling_input* endstop1, Prelling_input* endstop2,
		int homDirection, float home_speed, int home_timeout, float home_travel_mm, float home_travel_back_mm, float sensor_position) {
	uint32_t endtime;

	target_completeness = NaN; //can't have that here

	float tmpSpeed = stepper1->getMaxSpeed_mm();                  //save current motor speed for later
	stepper1->setMaxSpeed_mm(home_speed);                         //set homing fast speed for 1st travel
	stepper2->setMaxSpeed_mm(home_speed);                         //set homing fast speed for 1st travel
	stepper1->setCurrentPosition_mm(0.0f);                         //reset position to 0
	stepper2->setCurrentPosition_mm(0.0f);                         //reset position to 0
	stepper1->moveTo_mm(home_travel_mm * homDirection);           //run to endstop
	stepper2->moveTo_mm(home_travel_mm * homDirection);           //run to endstop
	endtime = millis() + home_timeout;
	bool endstop1_reach = false;
	bool endstop2_reach = false;
	while (!(endstop1_reach && endstop2_reach) && (millis() < endtime)) {              //block until endstop or timeout reached
		__WFI();
		if (!endstop1->get()) {
			stepper1->move(0);                                     //stepper shoud stop immediately
			endstop1_reach = true;
		}
		if (!endstop2->get()) {
			stepper2->move(0);                                     //stepper shoud stop immediately
			endstop2_reach = true;
		}
		job_prelling_handle();
	}
	if (millis() >= endtime) return;
	stepper1->move(0);                                            //stepper shoud stop immediately
	stepper2->move(0);                                            //stepper shoud stop immediately
	stepper1->setCurrentPosition_mm(0.0f);                         //reset position to 0
	stepper2->setCurrentPosition_mm(0.0f);                         //reset position to 0
	stepper1->moveTo_mm(home_travel_back_mm * homDirection * -1.0f); //go back a bit
	stepper2->moveTo_mm(home_travel_back_mm * homDirection * -1.0f); //go back a bit
	while (stepper1->isRunning() || stepper2->isRunning()) {                               //block until stepper reached position
		__WFI();
	    job_prelling_handle();
	}
	stepper1->setMaxSpeed_mm(home_speed / 6.0f);                     //set slow speed for 2nd forward motion
	stepper2->setMaxSpeed_mm(home_speed / 6.0f);                     //set slow speed for 2nd forward motion
	stepper1->moveTo_mm(home_travel_back_mm * 2.0f * homDirection);  //move to endstop 2nd time
	stepper2->moveTo_mm(home_travel_back_mm * 2.0f * homDirection);  //move to endstop 2nd time
	endtime = millis() + home_timeout / 2.0f;
	endstop1_reach = false;
	endstop2_reach = false;
	while (!(endstop1_reach && endstop2_reach) && (millis() < endtime)) {              //block until endstop or timeout reached
		__WFI();
		if (!endstop1->get()) {
			stepper1->move(0);                                     //stepper shoud stop immediately
			endstop1_reach = true;
		}
		if (!endstop2->get()) {
			stepper2->move(0);                                     //stepper shoud stop immediately
			endstop2_reach = true;
		}
		job_prelling_handle();
	}
	if (millis() >= endtime) return;
	stepper1->move(0);                                            //stepper shoud stop immediately
	stepper2->move(0);                                            //stepper shoud stop immediately
	stepper1->setCurrentPosition_mm(sensor_position);                         //homing finished
	stepper2->setCurrentPosition_mm(sensor_position);                         //homing finished
	stepper1->moveTo_mm(0.0f);
	stepper2->moveTo_mm(0.0f);
	stepper1->setMaxSpeed_mm(tmpSpeed);                           //restore motor speed
	stepper2->setMaxSpeed_mm(tmpSpeed);                           //restore motor speed
}


static void do_cmd_dwell(Gcode_command cmd) {
	if (cmd.valueT != NaN) {
		int milliseconds = round(cmd.valueT * 1000.0f);
		delay(milliseconds);
	}
}


static void do_cmd_set_position(Gcode_command cmd) {
	if (cmd.valueX != NaN) {
		stepperX.setCurrentPosition_mm(cmd.valueX);
	}
	if (cmd.valueY != NaN) {
		stepperY0.setCurrentPosition_mm(cmd.valueY);
		stepperY1.setCurrentPosition_mm(cmd.valueY);
	}
	if (cmd.valueZ != NaN) {
		stepperZ.setCurrentPosition_mm(cmd.valueZ);
	}
	if (cmd.valueE != NaN) {
		stepperE.setCurrentPosition_mm(cmd.valueE);
	}
	if (cmd.valueA != NaN) {
		stepperA.setCurrentPosition_mm(cmd.valueA);
	}
	if (cmd.valueB != NaN) {
		stepperB.setCurrentPosition_mm(cmd.valueB);
	}
	if (cmd.valueC != NaN) {
		stepperC.setCurrentPosition_mm(cmd.valueC);
	}
}


static void do_cmd_vacuum_pump(bool on) {
    output_pump.set(on);
}


static void do_cmd_vacuum_valve(bool on) {
	output_valve.set(on);
}
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

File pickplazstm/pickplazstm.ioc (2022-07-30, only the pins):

Mcu.UserName=STM32F411VETx
PC12.Signal=GPIO_Output
PB13.Signal=GPIO_Output
PD13.Signal=GPIO_Output
PD4.Signal=GPIO_Output
PB6.Signal=I2C1_SCL
PC7.Signal=GPIO_Output
PD0.Signal=GPIO_Output
PD8.Signal=GPIO_Input
PE5.Signal=GPIO_Output
PE1.Signal=GPIO_Output
PB2.Signal=GPIO_Output
PE13.Signal=GPIO_Input
PE2.Signal=GPIO_Output
PB7.Signal=I2C1_SDA
PE10.Signal=GPIO_Output
PE4.Signal=GPIO_Output
PB9.Signal=GPIO_Output
PB1.Signal=GPIO_Output
PA6.Signal=SPI1_MISO
PD12.Signal=GPIO_Output
PA10.Signal=USART1_RX
PC5.Signal=GPIO_Output
PD6.Signal=GPIO_Output
PD15.Signal=GPIO_Output
PB4.Signal=GPIO_Output
PA3.Signal=ADCx_IN3
PC11.Signal=GPIO_Output
PD3.Signal=GPIO_Output
PC8.Signal=GPIO_Output
PC4.Signal=GPIO_Output
PC6.Signal=GPIO_Output
PD7.Signal=GPIO_Output
PD1.Signal=GPIO_Output
PD9.Signal=GPIO_Input
PD5.Signal=GPIO_Output
PA0-WKUP.Signal=ADCx_IN0
PD10.Signal=GPIO_Input
PA13.Signal=SYS_JTMS-SWDIO
PA9.Signal=USART1_TX
PE11.Signal=GPIO_Output
PA1.Signal=ADCx_IN1
PB14.Signal=GPIO_Output
PA5.Signal=SPI1_SCK
PE14.Signal=GPIO_Input
PE15.Signal=GPIO_Input
PE6.Signal=GPIO_Output
PE0.Signal=GPIO_Output
PE12.Signal=GPIO_Output
PA2.Signal=ADCx_IN2
PD14.Signal=GPIO_Output
PA4.Signal=GPIO_Output
PB5.Signal=GPIO_Output
PD11.Signal=GPIO_Output
PA11.Signal=GPIO_Input
PA14.Signal=SYS_JTCK-SWCLK
PE3.Signal=GPIO_Output
PB8.Signal=GPIO_Output
PC9.Signal=GPIO_Output
PD2.Signal=GPIO_Output
PB0.Signal=GPIO_Output
PB12.Signal=GPIO_Input
PA7.Signal=SPI1_MOSI

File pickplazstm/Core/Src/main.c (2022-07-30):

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
/* Includes ------------------------------------------------------------------*/
#include "main.h"

/* USER CODE BEGIN Includes */
#include "app.h"
/* USER CODE END Includes */

ADC_HandleTypeDef hadc1;

I2C_HandleTypeDef hi2c1;

SPI_HandleTypeDef hspi1;

TIM_HandleTypeDef htim2;
TIM_HandleTypeDef htim3;
TIM_HandleTypeDef htim4;

UART_HandleTypeDef huart1;
DMA_HandleTypeDef hdma_usart1_rx;

void SystemClock_Config(void);
static void MX_GPIO_Init(void);
static void MX_DMA_Init(void);
static void MX_ADC1_Init(void);
static void MX_SPI1_Init(void);
static void MX_USART1_UART_Init(void);
static void MX_I2C1_Init(void);
static void MX_TIM2_Init(void);
static void MX_TIM3_Init(void);
static void MX_TIM4_Init(void);
/**
  * @brief  The application entry point.
  * @retval int
  */
int main(void)
{
  /* MCU Configuration--------------------------------------------------------*/

  /* Reset of all peripherals, Initializes the Flash interface and the Systick. */
  HAL_Init();

  /* Configure the system clock */
  SystemClock_Config();

  /* Initialize all configured peripherals */
  MX_GPIO_Init();
  MX_DMA_Init();
  MX_ADC1_Init();
  MX_SPI1_Init();
  MX_USART1_UART_Init();
  MX_I2C1_Init();
  MX_TIM2_Init();
  MX_TIM3_Init();
  MX_TIM4_Init();
  /* Infinite loop */
  /* USER CODE BEGIN WHILE */
  setup();

  HAL_TIM_Base_Start_IT(&htim2);  //timer has no used interrupt, but counter counts in 1us interval and overflows after 2^32
  htim3.Instance->ARR = 20-1;
  HAL_TIM_Base_Start_IT(&htim3);  //25us timer for fast program handling stuff
  htim4.Instance->ARR = 1000-1;
  HAL_TIM_Base_Start_IT(&htim4);  //1ms  timer for time program handling stuff

  while (1)
  {
	  __WFI();
	  loop();
    /* USER CODE END WHILE */

    /* USER CODE BEGIN 3 */
  }
  /* USER CODE END 3 */
}

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


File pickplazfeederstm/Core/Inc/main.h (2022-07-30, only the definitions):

#define FEED_Pin GPIO_PIN_3
#define FEED_GPIO_Port GPIOA
#define OPTO_INTERRUPT_Pin GPIO_PIN_4
#define OPTO_INTERRUPT_GPIO_Port GPIOA
#define OPTO_LED_Pin GPIO_PIN_5
#define OPTO_LED_GPIO_Port GPIOA
#define MOT_NEG_Pin GPIO_PIN_6
#define MOT_NEG_GPIO_Port GPIOA
#define MOT_POS_Pin GPIO_PIN_7
#define MOT_POS_GPIO_Port GPIOA
#define SW_FORWARD_Pin GPIO_PIN_2
#define SW_FORWARD_GPIO_Port GPIOB
#define SW_BACKWARD_Pin GPIO_PIN_10
#define SW_BACKWARD_GPIO_Port GPIOB
#define LED4_Pin GPIO_PIN_11
#define LED4_GPIO_Port GPIOB
#define LED3_Pin GPIO_PIN_8
#define LED3_GPIO_Port GPIOA
#define LED2_Pin GPIO_PIN_9
#define LED2_GPIO_Port GPIOA
#define LED1_Pin GPIO_PIN_10
#define LED1_GPIO_Port GPIOA
#define LED0_Pin GPIO_PIN_11
#define LED0_GPIO_Port GPIOA
#define TP1_Pin GPIO_PIN_3
#define TP1_GPIO_Port GPIOB
#define TP2_Pin GPIO_PIN_4
#define TP2_GPIO_Port GPIOB
#define TP3_Pin GPIO_PIN_5
#define TP3_GPIO_Port GPIOB
#define TP4_Pin GPIO_PIN_6
#define TP4_GPIO_Port GPIOB
#define TP5_Pin GPIO_PIN_7
#define TP5_GPIO_Port GPIOB

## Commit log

2021-03-21 added camera
2021-05-29 stm32 project
2021-05-30 more interrupt speed
2021-05-30 stepper speed optimization, protocol bugfix on negative numbers
    [AccelStepperExtended.cpp, app.cpp, arduino_like_hal.cpp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]
2021-05-30 pindefinition for new board revision. Stepper driver microstepping in initialization. cleanup.
2021-05-30 optimized interrupts
2021-06-01 fix gcode parser bug
    [uart_handler.cpp]
2021-07-19 pcb+gerber first checkin
    [pcb-pick-plaz-guide.brd, pcb-pick-plaz-guide.sch, pcb-pick-plaz-led.brd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]
2021-07-19 control board as ordered
    [pcb-pick-plaz-control_v1d.brd, pcb-pick-plaz-control_v1d.sch]
2021-07-19 pcb revision E (includes microstep sel wiring)
    [pcb-pick-plaz-control_v1e.brd, pcb-pick-plaz-control_v1e.sch]
2021-07-19 debug homing
2021-07-19 removed print
2021-07-19 improve homing
2021-07-19 uart protocol
2021-07-25 pcb missing trace fix
    [pcb-pick-plaz-ring.brd]
2021-07-25 camera gcode
2021-07-29 material icons from google
2021-07-30 added camera calibration scripts
2021-07-30 changed serial port to raspberrypi port
2021-07-30 added test calibration test gui
2021-07-30 Invoked calibration in gui
2021-07-30 added setpos event, invoke bottle server from pcb_cal
2021-07-31 first simple camera fetch
2021-07-31 show camera checkbox
2021-07-31 center camera & FHD gui fix
2021-07-31 more footprints
2021-08-01 fix motor steps/mm
2021-08-01 lamp on camera + robot test + bugfix Firmware
    [app.cpp]
2021-08-01 scale of web camera
2021-08-01 fixed calibration scale
2021-08-01 added ficucial search prototype
2021-08-01 change pcb coordinate to nav.json
2021-08-01 pnp_bom_parser & data.json for small led ring
2021-08-01 added pcb fiducial interface
2021-08-02 gui and unassign button
2021-08-02 added pcb calibration with 2 fiducial
2021-08-02 removed print statement
2021-08-02 fix endstop speed and lower robot speed
    [app.cpp]
2021-08-09 motor speed and z homing
2021-08-09 fix speed re-assignment after home failed
    [app.cpp]
2021-08-14 aruco pcb
    [pcb-pick-plaz-aruco v1.brd, pcb-pick-plaz-aruco v1.sch]
2021-08-14 hall pcb
    [pcb-pick-plaz-hall v1.brd, pcb-pick-plaz-hall v1.sch]
2021-08-28 added mock camera
2021-08-28 pnp bom upload
2021-08-28 added default calibration
2021-08-29 added centered pcb
2021-08-29 gui elements in place, bom parser fix
2021-08-29 fix and test debug case
2021-08-29 milling code for button-up
2021-08-29 aruco & hall pcb + gerber
    [pcb-pick-plaz-aruco v1.brd, pcb-pick-plaz-aruco v1.sch, pcb-pick-plaz-hall v1.brd]
2021-09-05 calibrate picker button
2021-09-05 added calibration with second tilted pattern
2021-09-07 improved picker logic, added picker calibrate
2021-09-07 refactoring context->bom->part->designator
2021-11-01 improved picker calibration
2021-11-07 refactoring, added belt draft
2021-12-04 footprints revision
2022-01-22 led polarity indicator
2022-01-22 footprint alternative list
2022-01-22 automatic footprint detection
2022-01-22 reset board, gui improvements
2022-01-23 picker calibration template handling
2022-01-23 reset pcb part states
2022-01-23 utf-16 bom from easyeda parsing
2022-01-23 improved belt handling, bugfix, fiducial feature
2022-06-09 belt feeder refinement
2022-06-11 bed new head
2022-06-11 feeder positions, bed bounds
2022-06-11 bed definition, indent
2022-06-11 drawing of bed shapes
2022-06-12 tray light switching
2022-06-12 picker calibration light
2022-06-12 belt feeder position modify
2022-06-12 belt drawing
2022-06-13 trinamic drivers on supportive axies
2022-06-13 move overlap STM32
2022-06-14 stepper tune, placing
2022-06-14 dwell timer before taking pictures
2022-07-23 feeder pcb
    [pcb-pick-plaz-feeder-wiring.brd, pcb-pick-plaz-feeder-wiring.sch, pcb-pick-plaz-feeder.brd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]
2022-07-24 stm32 project for feeder
2022-07-24 fix pcb bed centering
2022-07-24 slower static belt picking
2022-07-30 bottom led
2022-07-31 separate holefinder and roll feeder logic
2022-07-31 only camera mode
2022-08-01 fan gpio with off delay
2022-08-01 feeder advance before camera
2022-08-11 updated pcbs with step files
    [pcb hall.step, pcb-pick-plaz-control_v1e.brd, pcb-pick-plaz-control_v1e.sch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]
2022-08-11 link to cad repository
2023-08-25 feeder schematic
2023-11-20 data parser and test cases
    [Labclock.csv, Labclock_BOM.csv]
2023-12-23 bugfix and temporary fix for Z motor drift

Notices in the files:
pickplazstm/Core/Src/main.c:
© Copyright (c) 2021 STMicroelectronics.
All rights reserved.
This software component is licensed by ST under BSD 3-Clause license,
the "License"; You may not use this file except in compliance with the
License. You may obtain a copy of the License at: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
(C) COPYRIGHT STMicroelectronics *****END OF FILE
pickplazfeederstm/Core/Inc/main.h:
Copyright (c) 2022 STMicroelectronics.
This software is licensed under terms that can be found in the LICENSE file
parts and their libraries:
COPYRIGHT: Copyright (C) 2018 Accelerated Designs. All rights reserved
